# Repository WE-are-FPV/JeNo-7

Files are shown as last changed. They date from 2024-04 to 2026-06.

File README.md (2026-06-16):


> [!NOTE]
> Current version : **1.1.1** (read [changelog](#changelog) for details)

<!--![JeNo - Front view](./images/JeNo7_CloseProfileHeader.jpg)-->

# JeNo 7"
***7" drone FPV frame compatible with Air Unit O3 and O4 Pro, designed for LR, Cinematic, Freeride and even Freestyle. Many customizable options available.***

> [!NOTE]
> Designed in France by members of the [WE are FPV](https://www.wearefpv.fr/) community. The French version of the project is available on [Printables](https://www.printables.com/fr/model/847975-jeno-7-drone-frame). Note that a [2.5" version](https://github.com/WE-are-FPV/JeNo-Pocket), [3-3.5" version](https://github.com/WE-are-FPV/JeNo-3-3.5) and a [5.1-6" version](https://github.com/WE-are-FPV/JeNo-5.1) of the JeNo exist.

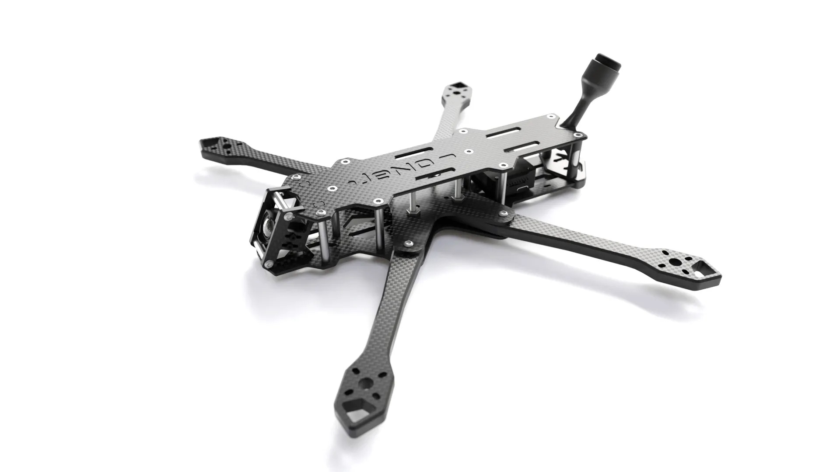
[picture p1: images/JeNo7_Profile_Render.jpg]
JeNo classic - 3D render


## Table of contents

* [Key features](#key-features)
* [Presentation](#presentation)
* [Detailed specifications](#detailed-specifications)
* [Versions and files](#versions-and-files)
* [Customization](#customization)
* [Cut it !](#cut-it-)
* [Bill of materials](#bill-of-materials)
* [Building/Assembly guide](#buildingassembly-guide)
* [Inspiration](#inspiration)
* [Tuning, Betaflight Preset ?](#tuning-betaflight-preset-)
* [Blackbox](#blackbox)
* [Videos](#videos)
* [Builds examples](#builds-examples)
* [Authors](#authors)
* [TPU](#tpu)
* [Community (remixes and TPU)](#community-remixes-and-tpu)
* [Changelog](#changelog)

## Key features
- [x] **Sturdiness** and **rigidity** (6 or 8 mm arms)
- [x] Designed as a **real 7"**, not 5" conversion
- [x] Excellent flight **performances**, easy to tune
- [x] **Wide-X** geometry
- [x] Perfect DJI **Air Unit O3 or O4 Pro** camera integration
- [x] Designed for : DJI Vista/AU O3/AU O4 Pro, WalkSnail, HDZero, Analogic
- [x] **Frame and standoffs NOT visible** in video feed, with any FPV camera
- [x] Stack **decoupled** from the arms
- [x] **Easy maintenance** : remove 3 screws to replace an arm
- [x] **Roomy** (30 mm high)
- [x] **Customizable** (arms thickness, camera plates)

## Presentation
Building on the success of the [5.1-6" version](https://github.com/WE-are-FPV/JeNo-5.1) and [3-3.5" version](https://github.com/WE-are-FPV/JeNo-3-3.5) versions, the **JeNo lineup** expands with this new variation in **7-8"**. We stay true to the JeNo spirit, offering a **versatile frame** that is perfect for **Long Range, cinematic**, and even **Freestyle** use, thanks to its strength and flight performance.

Given the limited options in the **Open Source** community for 7", especially for DJI O3/O4 Pro setups, we wanted to provide the community with a solid new option that caters to various needs while remaining true to the **"JeNo philosophy"** :

* **Clean Black Box** for easy tuning
* **Modularity**, with **8mm arms** (or 6mm with reinforcements) and a wide range of camera plates:
  - Classic at 25°
  - High tilt at 40°
  - Cinematic with clean FOV ("Wide") / 25° tilt (hard or soft)
  - Cinematic with clean FOV ("Wide") / 40° tilt
* Frame and standoffs invisible in the video feed with all cameras
* **100% clear FOV** with DJI O3/O4 Pro setups with cinematic camera plates (no frame or propellers visible)
* **Wide X** geometry for better flight feel
* Comfortable body for lipos up to over 6S / 3000mAh (+140mm available)

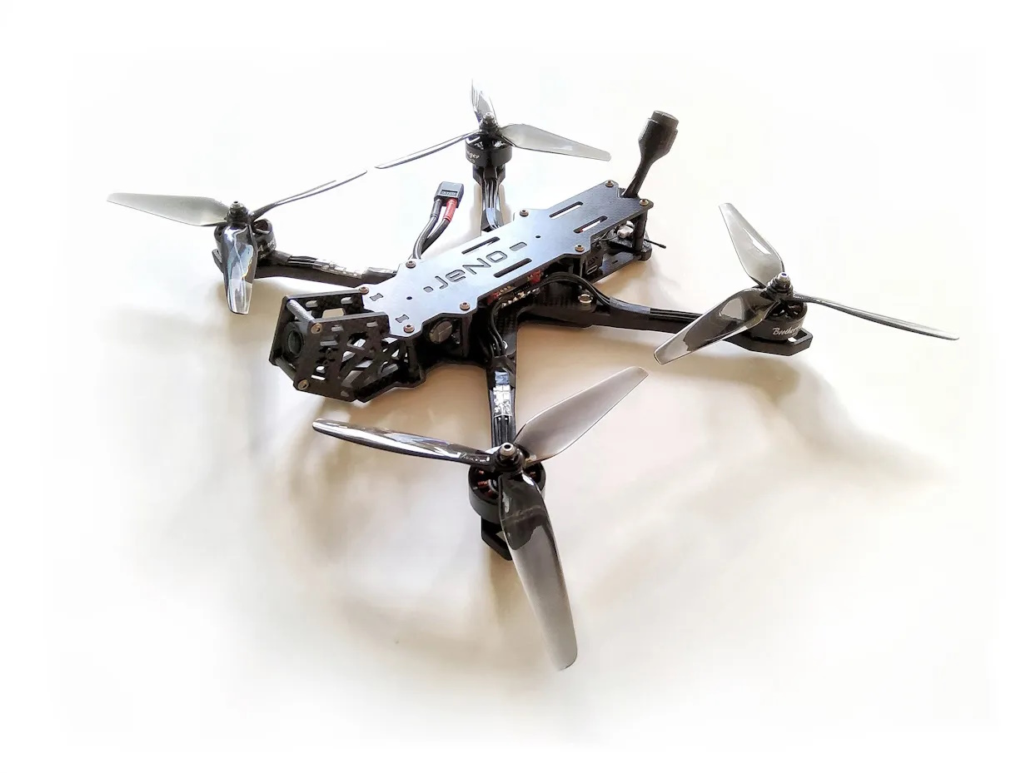
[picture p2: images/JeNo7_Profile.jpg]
JeNo 7 Profile


Finally, since this frame was designed by members of the [WE are FPV](https://www.wearefpv.fr/) **community**,  the "WaF" logo is engraved under the bottom plate (feel free to keep it or not). Join us on the WAF forum in [the official JeNo 7" thread](https://forum.wearefpv.fr/topic/22687-jeno-7/) to discuss it further.

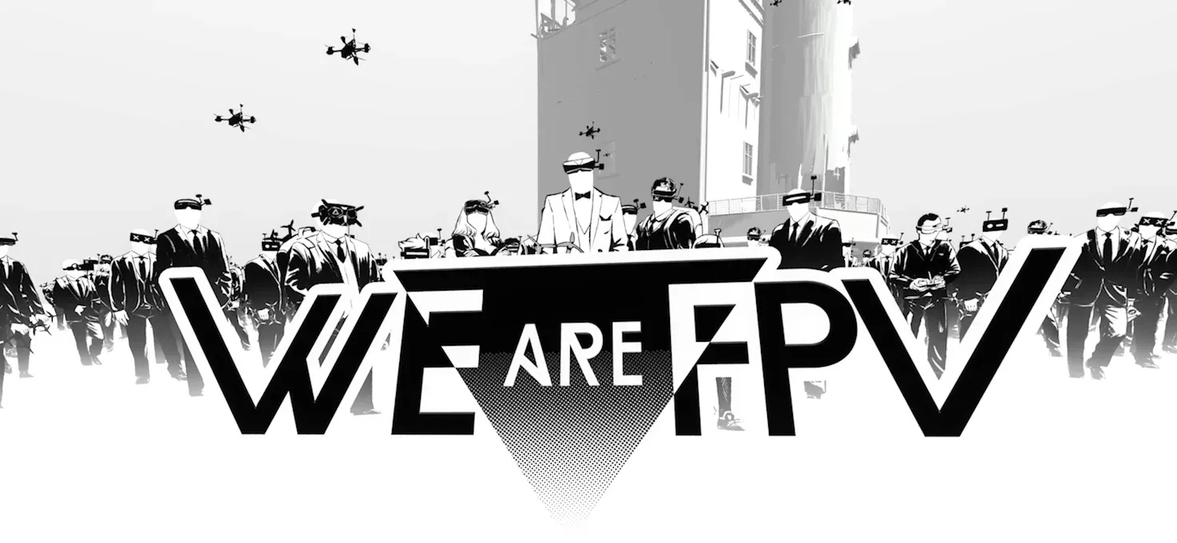
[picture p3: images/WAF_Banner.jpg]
WE are FPV banner


The JeNo is also available in [2.5" version](https://github.com/WE-are-FPV/JeNo-Pocket), [3" and 3.5" version](https://github.com/WE-are-FPV/JeNo-3-3.5) and [5.1" and 6" version](https://github.com/WE-are-FPV/JeNo-5.1).

## Detailed specifications

||| 
| :--- | :--- |
| **Geometry** | **Wide-X** | 
| **Props size** | 7" | 
| **Weight** | **248 to 260 g** depending on the versions, including screws | 
| **Arms** | **6 mm** (with 4mm reinforcements), **8mm** | 
| **Body height** | 30 mm | 
| **Stack height** | 19.5 to 21.5 mm depending the arms heights | 
| **Bottom plate** | 3mm | 
| **Middle plate** | 2.5 mm | 
| **Top plate** | 2.5 mm | 
| **Camera plates** | 3 mm | 
| **Motors mounting** | 16 to 19 mm | 
| **Camera** | 20 mm (DJI), Micro, Nano. **Clear FOV**. Ajustable.
| **Main stack** | 30 mm x 30 mm (M3) and 20 mm x 20 mm (M3) stack | 
| **Back stack** | 20 mm x 20 mm and 25 .5 x 25.5 mm | 
| **Supported VTX** | Analogic, DJI Vista, DJI Air Unit O3/O4 Pro, WalkSnail, HDZero… | 
| **Strap passage** | Yes | 

## Versions and files

### Versioning
You will find the **current version** of the frame at the beginning of the description and the full [history of modifications](#changelog) at the end of the page.

We strongly recommend always cutting the latest version to ensure you benefit from the most recent optimizations.

The version **number format** is as follows :
```
<Major versions>.<Minor version>.<Revision>
ex : 1.3.2
```

* **Revision :** This number is incremented in the case of minor modifications with no significant impact.
* **Minor version :** This number is incremented for minor modifications that may potentially break compatibility with certain TPU parts.
* **Major version :** This number is incremented for significant modifications that break compatibility at the carbon level.

Since the creation of the JeNo 7", we have always strived to **maintain compatibility at the carbon level**. As a result, the version remains “1.x.y.”

In practical terms, this means that if you have the very first version of the JeNo 7" and want to equip it with the **O4 Pro**, you only need to have new camera plates cut—they will be compatible with your frame version!

**Note :** If you develop TPU parts for the JeNo, be sure to specify the version they are compatible with.

### Files management
To simplify things, we have reorganized the file structure. The files are now divided into **five groups** :

* **01-FRAME :** Contains **models** describing the **frame** in DXF, STEP, and STL formats for the current version. Also contains a PDF file which is a reformatted version of the DXF.
* **02-TPU :** Contains **TPU models** for the current frame version in STL format.
* **03-FRAME-HISTORY :** Contains previous versions of the frame.
* **04-TPU-HISTORY :** Contains TPU models that are no longer compatible with the current version.
* **OTHER-FILES :** Contains documentation files. No assembly manual at the moment, but can check the [assembly guide of the JeNo 5"](https://github.com/WE-are-FPV/JeNo-5.1/tree/main/OTHER-FILES) which is very similar.

The major change is that all options are now consolidated into a single file. This will make version management significantly easier for us.

If you want to view the DXF file with all annotations, we recommend using the free software [DWG TrueView](https://www.autodesk.com/products/dwg-trueview/overview). If you prefer not to use it, the PDF version of the file will contain all the necessary information.

## Customization
As usual, this JeNo is **customizable** : it offers several **options** to best adapt to different needs and preferences.

### The arms
> [!TIP]
> We **strongly recommend** having the version with **8mm** arms cut (see Black Box a little further down). 

However, the version with 6mm + reinforcements remains entirely viable in case you have constraints on the availability of 8mm carbon.

The weight of the two versions remains very similar.

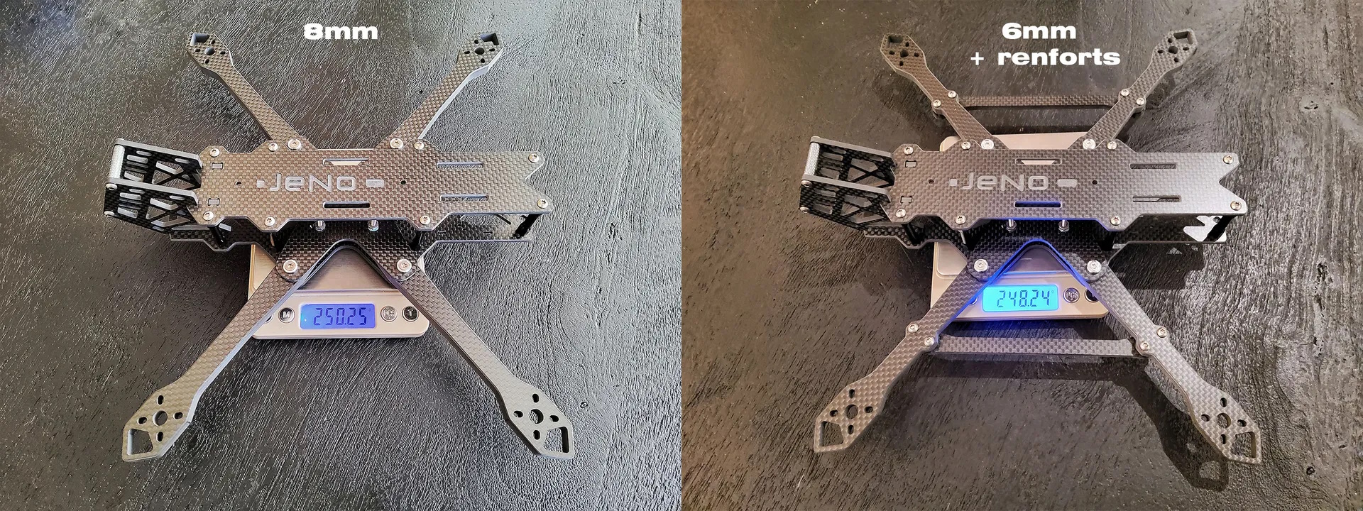
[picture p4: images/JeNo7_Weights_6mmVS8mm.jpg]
JeNo 7 weights


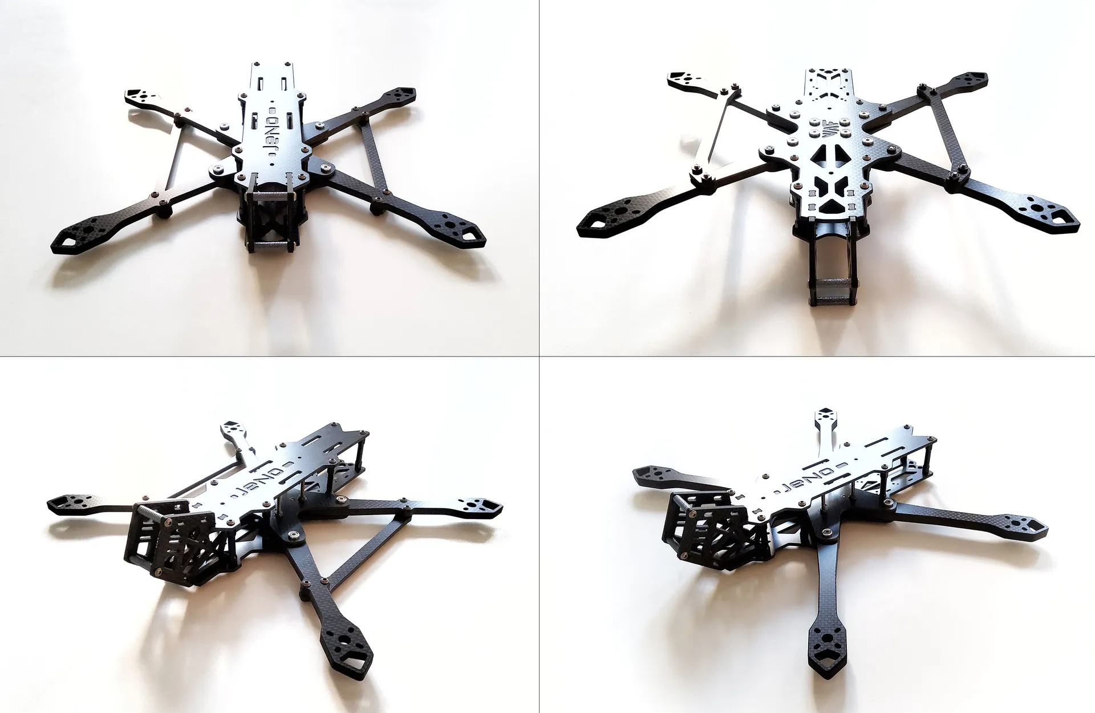
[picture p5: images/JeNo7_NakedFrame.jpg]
JeNo 7 verions


### Camera plates and O3 integration

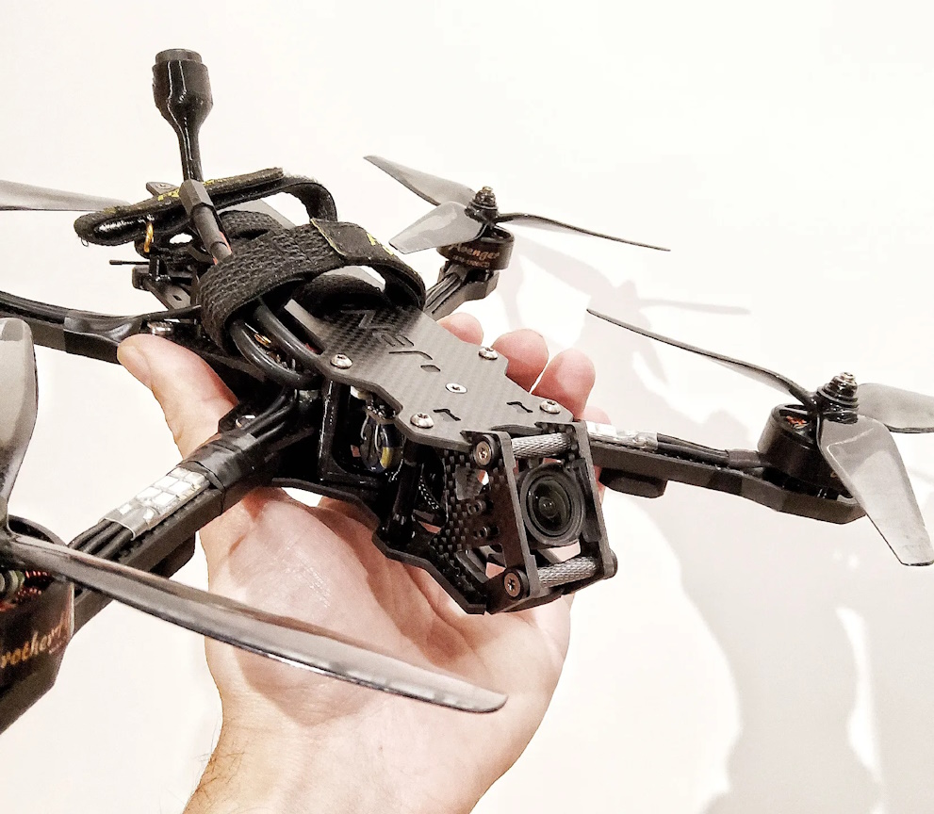
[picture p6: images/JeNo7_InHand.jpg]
JeNo 7 Cmera Plates


> [!CAUTION]
> The use of a 200mm coaxial cable for the O3 camera is mandatory.

Remarks regarding the **PWM frequency** of ESCs:

* **DJI recommends** using a PWM frequency of **48 kHz** or higher for effective stabilization
* However, a PWM frequency of **24 kHz is generally recommended for 7"**
* We have not observed stabilization issues while remaining at 24 kHz, even with a "hard mounted" camera. Therefore, we encourage you to test 24 kHz before anything higher.

Comparison of **FOV settings** with specific 7" Cinematic camera plates (Ultra Wide vs Wide):

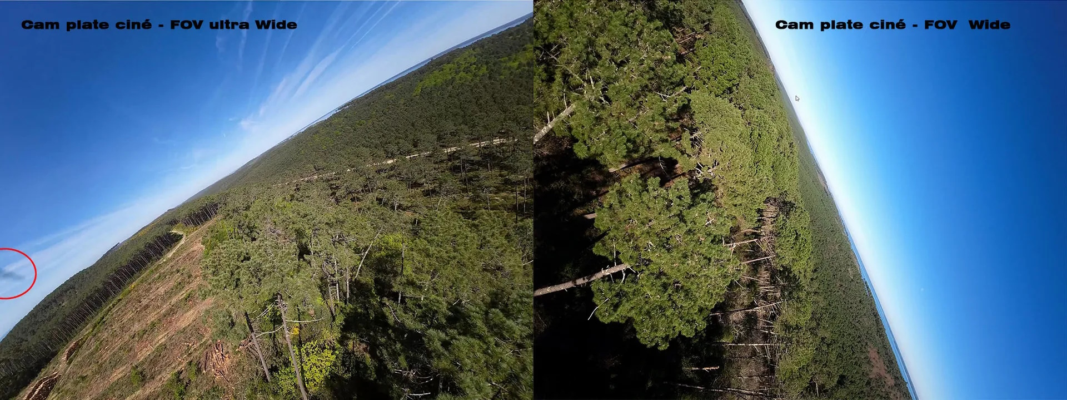
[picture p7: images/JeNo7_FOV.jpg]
JeNo 7 Camera Plates


The "cinematic" camera plates will allow you to enjoy a completely clear FOV (set as **Wide** in the O3) (and consequently, after stabilization).

Several types of camera plates are available, so you will need to **choose** the type of camera plate that best suits **your needs**.

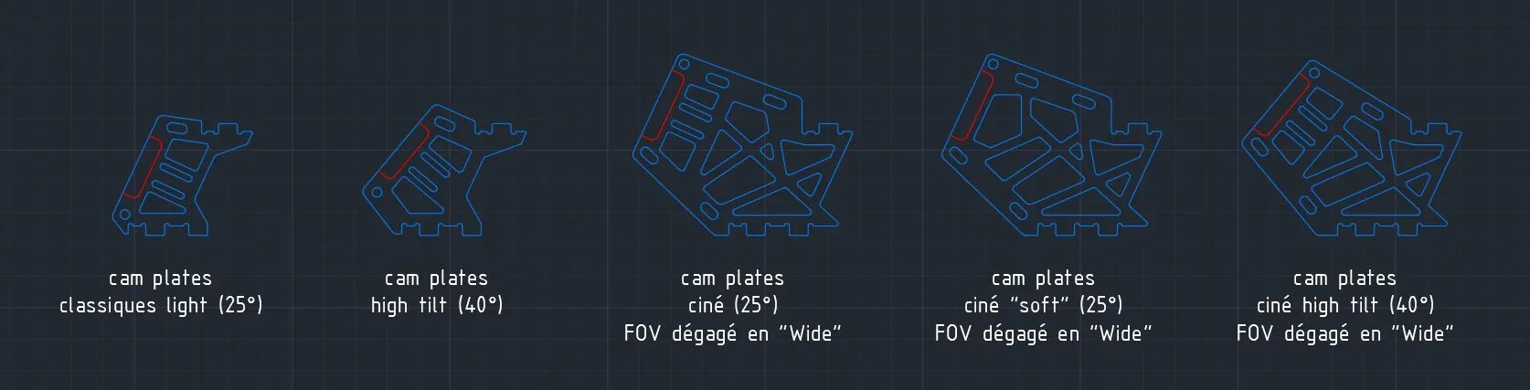
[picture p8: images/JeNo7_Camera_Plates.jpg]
JeNo 7 Camera Plates blue prints


## Cut it !

The JeNo 7" is available from [CNC Madness](https://cncdrones.com/jeno-7-inch.html) (Canada) and [FPV CNC Drone](https://fpvcncdrone.com/) (France).

The ["01-FRAME"](https://github.com/WE-are-FPV/JeNo-7/tree/main/01-FRAME) folder contains all the files you need to get it **cut** in your favourite flavour.

Consult the **DXF file** of the frame (or the PDF version) to choose the version that interests you.

Feel free to select a pre-made "Edition" (Classic, Light, or Bando), or mix different options and choose certain "extras".

You will also need to choose a type of camera plates (classic, cine, etc.).

> [!NOTE]
> All parts versions are compatible with each others

## Bill of materials

In addition to the carbon fiber, you will need the following hardware to complete the assembly of the frame.

**Standoffs**

It is recommended to use 5mm diameter standoffs, especially for those that will serve as support for TPU (backpack and capacitor). Moletted spacers can still be used, but the TPU supports will need to be modified accordingly.

| Quantity | Description | Details |
| :---: | :--- | :--- |
| 10 | M3x30mm standoffs | for the body |
| 2 (or 4 for cinematic plates) | M3x20mm standoffs | for the camera |

**Stack materials**

* If 30x30 stack

| Quantity | Description | Details |
| :---: | :--- | :--- |
| 4 | M3x20mm countersunk screws | for the stack |
| 4 | M3 nuts for stack screws | |

* If 20x20 stack

| Quantity | Description | Details |
| :---: | :--- | :--- |
| 4 | M3x20mm countersunk screws | for the stack |
| 4 | M3 nuts for stack screws | |

**Frame materials**

| Quantity | Description | Details |
| :---: | :--- | :--- |
| 6 | M3x6/8mm countersunk screws | for the top plate |
| 4 | M3x6/8mm screws | for the top plate |
| 10 | M3x8mm screws (titanium if possible) | Bottom plate |
| 4 (or 8 for cinematic plates) | M3x6/8mm screws (titanium if possible) | Camera plates |
| 12 | Pressnuts ([Flywoo](https://www.drone-fpv-racer.com/flywoo-m3-clinch-nuts-20-pcs-7965.html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) or SourceOne alike) | |
| 4 | M3x18mm countersunk screws + washers or M3x16mm screws (steel if possible)  | for the arms (2 mm shorter for 6mm arms) |
| 4 | M3x12mm countersunk screws + washers or M3x10mm screws (steel if possible) | for the arms (2 mm shorter for 6mm arms) |

**Additional materials 6mm amrs  renforcements**

| Quantity | Description | Details |
| :---: | :--- | :--- |
| 8 | Pressnuts ([Flywoo](https://www.drone-fpv-racer.com/flywoo-m3-clinch-nuts-20-pcs-7965.html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) or SourceOne alike) | 2 per arm) |
| 8 | M3x12mm screws | 2 per arm |

**Additional materials**

| Quantity | Description | Details |
| :---: | :--- | :--- |
| 16 | M3x12mm screws (if using arms protections) or M3x8mm (if no TPU) | for the motors (2 mm shorter for 6mm arms) |
| 4 | M2x5mm screws | for the camera |

**Fasten the lipo**

The JeNo allows the use of non-slip straps thanks to its strap slots. You can also use a LiPo pad if desired.

## Building/Assembly guide

Find numerous examples of builds on the _**DroneBuilds**_ page of WE are FPV.
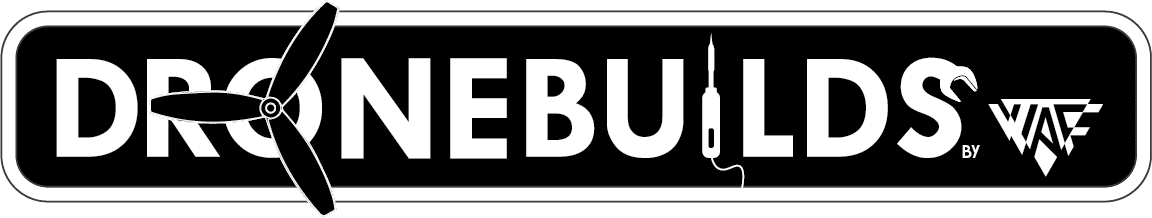
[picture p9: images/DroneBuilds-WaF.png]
DroneBuilds (https://forum.wearefpv.fr/71-dronebuilds/ "DroneBuilds - Click to Access!")


The assembly of the frame is straightforward; however, a few clarifications:

* On one of the two sides of the **middle plate**, there are countersunk holes to accommodate countersunk screws. This side corresponds to the **underside**. Do not forget to install the stack screws before installing the middle plate.
* The pressnuts will be positioned on the underside of the bottom plate.
* An RX T antenna can be fixed to the rear of the JeNo using zip ties.
* Six screws of the top plate are countersunk screws to avoid damaging the battery.

## Inspiration
The JeNo 7" takes inspiration from the path laid out by the [KayouLoin](https://kayou-frames.com/fr/frames/25-kayouloin-7-frame.html).

While implementing 8mm arms remains quite evident, the KayouLoin innovates by introducing a **body that matches the quad's proportions**.

Certainly, this adds weight, but it provides the frame with unparalleled comfort in accommodating suitable batteries and absolute rigidity. If the cutting and sourcing of hardware are too constraining for you, we advise you to go directly to [Kayou's website](https://kayou-frames.com/fr/) !

## Tuning, Betaflight Preset ?
We probably won't provide a preset because motor setups have a huge influence, but here are some recommendations from Mark Spartz for 7" setups:

* ESCs PWM Frequency at **24KHz**
* **Reduce I** compared to a 5" (start with the slider at 0.5)

## Blackbox

Here is an overview of vibration distribution on the 3 axes for the JeNo 7". On the right with 6 mm arms (+ reinforcements), on the left with 8 mm arms. This is indeed the **unfiltered** gyro signal for a 3 minutes freestyle flight :

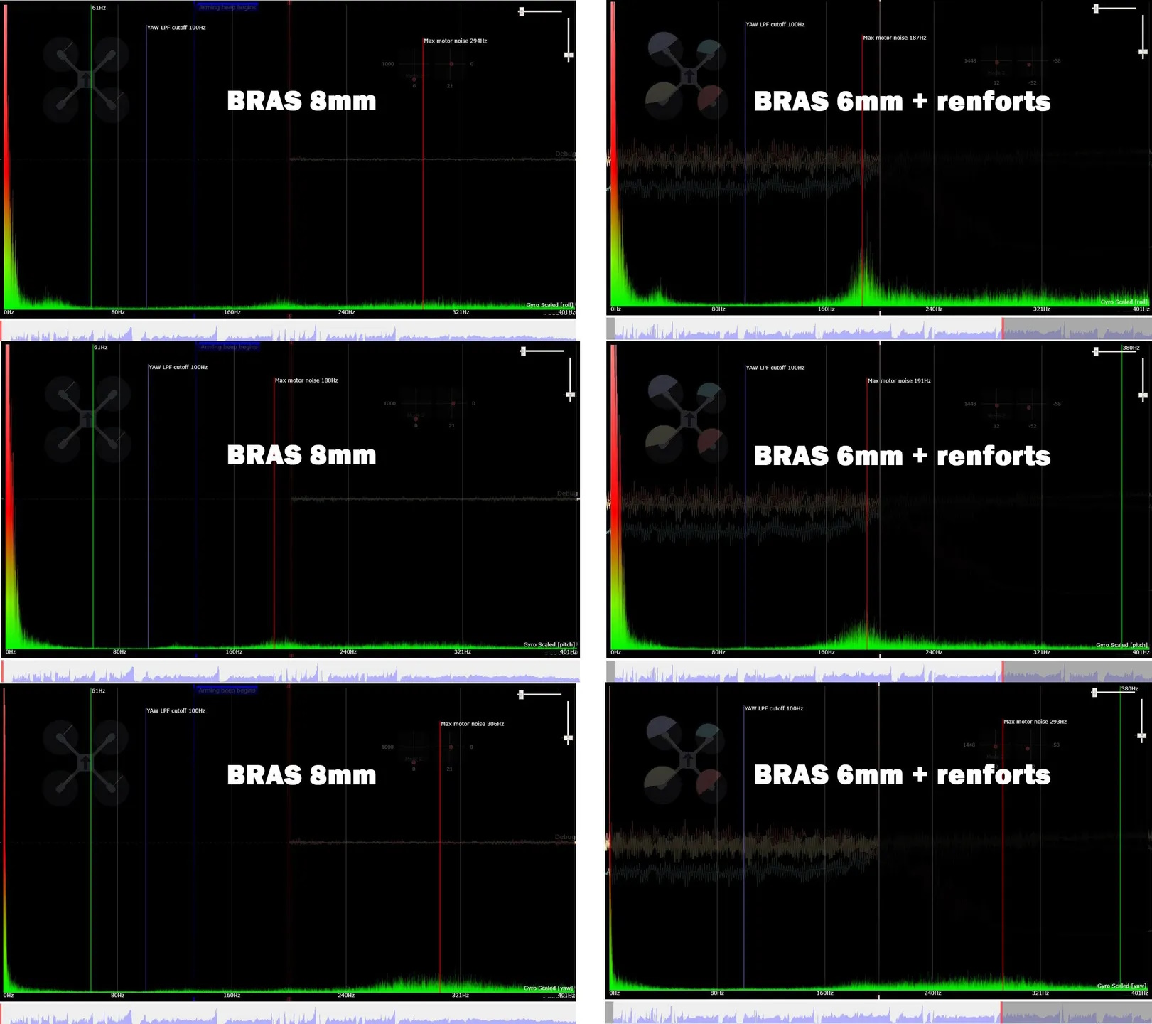
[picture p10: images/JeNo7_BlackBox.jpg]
JeNo 7 Blackbox


## Videos
Freestyle with JeNo :

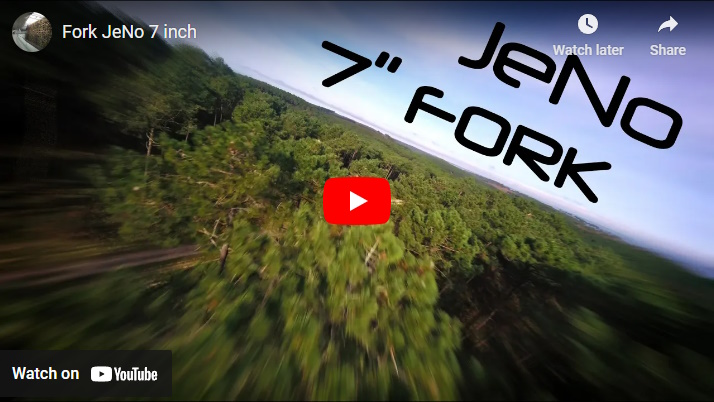
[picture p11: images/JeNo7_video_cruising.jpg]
JeNo 7" Maiden (https://www.youtube.com/watch?v=4mE-WnIyyHg "JeNo 7 Maiden - Click to Watch!")


## Builds examples
You can find build examples on [WE are FPV's DroneBuilds](https://forum.wearefpv.fr/71-dronebuilds/) :

* fr : [JeNo 7" Fork](https://forum.wearefpv.fr/topic/22645-jeno-7-fork)

## Authors

The JeNo was designed by :

* nochamo - [Youtube](https://www.youtube.com/user/nochamo)

## TPU
For now, a [minimalist TPU kit](https://github.com/WE-are-FPV/JeNo-7/tree/main/tpu) is available to you, containing:

* O3 antenna mount
* Double SMA Antenna Support
* 50V capacitor mount + spike absorber
* Rear bumper + RX antenna mount
* Front RX Support
* Arm protection with skids (6 and 8mm)

This offering **will expand** over time thanks to the community.

## Community (remixes and TPU)

**Fork/remix**

* [JeNo 7" Freestyle (Bash Edition)](https://www.printables.com/model/1073983-jeno-7freestyle-bash-edition), a mix between the JeNo 7" and the [JeNo PlatyStyle](https://www.printables.com/model/744619-jeno-51-platystyle-edition), otpimised for freestyle, by [Bash FPV](https://www.youtube.com/watch?v=s_6Gz9fyeIc&ab_channel=BashFPV)
* [JeNo 7" BBL - Freestyle Bando - RanxFPV Edition](https://www.printables.com/model/1411549-jeno-7-bbl-freestyle-bando-ranxfpv-edition), a mix between the JeNo 7" and the remix from Bash FPV, for freestyle and bando (O3 and O4 Pro compatible), by [RankFPV](https://www.youtube.com/@RanxFPV)

**TPU**

In addition to the TPU options available on this page, you will find here some TPU designs created by the community.

* [Full TPU set](https://www.printables.com/fr/model/911148-jeno-7-tpu-kit-complet), [immortal-T antenna support](https://www.printables.com/fr/model/914154-jeno7-antenne-immortal-t) and a [DJI Action 2 mount](https://www.printables.com/fr/model/918051-jeno-7-dji-action-2-mount-25deg-filtre-nd-tbs) designed by [Jean-Lil](https://www.printables.com/fr/@JeanLil_707453)
* [Full TPU set, compatible with COB LEDs](https://makerworld.com/en/models/551901) by [BinaryWhite](https://www.youtube.com/@focal3drone803) (many TPUs are available, including RX and GPS mounts)
* [DJI Action 2 mount](https://www.printables.com/fr/model/960035-jeno-7-dji-action-2-mount-40deg-filtre-nd-tbs-batm) with a 40-degrees-tilt by [Lëtz Kwad](https://www.printables.com/fr/@LetzKwad_707453)

## Changelog

> [!TIP]
> Compatibility is consistently maintained between each version: if your frame was a v1, the parts from v1.2 will be compatible. The same applies to TPU accessories. That's why we don't keep the history of previous versions.

* 18/02/2025 :
  * Addition of TPU for softmounted camera plates (compatible with O4 Pro and O3)
* Version **1.1.1** (02/02/2025) :
  * Addition of cinematic and softmounted camera plates at 25° (for O4 Pro and O3)
* Version **1.1.0** (01/02/2025) :
  * Support for the Air Unit O4 Pro (camera plates)
* 21/05/2024 :
  * Addition of a top plate with XT60 cutout in the "extra" folder
* 04/06/2024 : 
  * Addition of 8" arms (untested) in the "extra" folder
* Version **1.0.0** (23/04/2024)

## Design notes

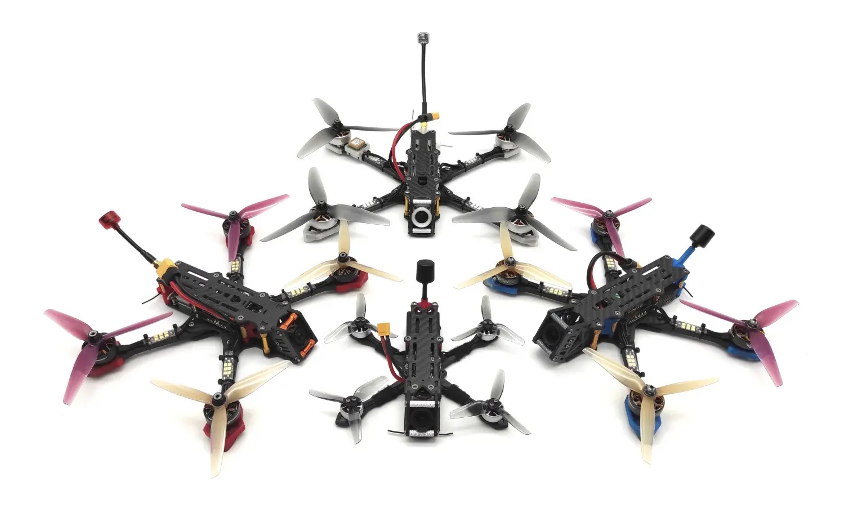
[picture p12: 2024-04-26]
images/JeNo_Family.jpg

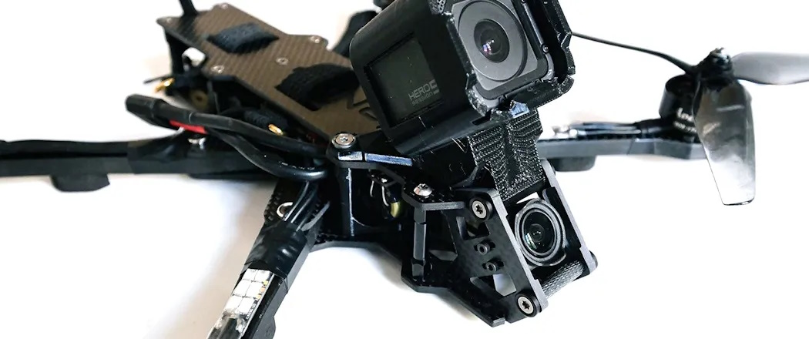
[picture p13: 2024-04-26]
images/JeNo7_CloseProfileHeader.jpg

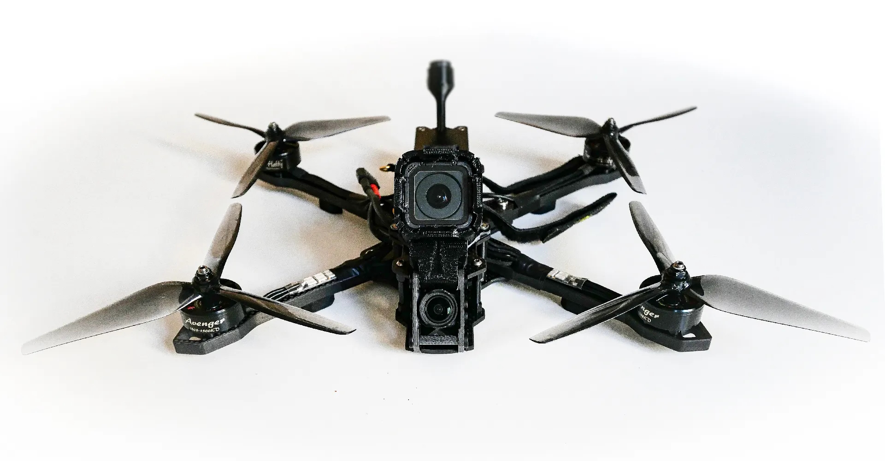
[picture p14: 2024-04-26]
images/JeNo7_TopFront.jpg

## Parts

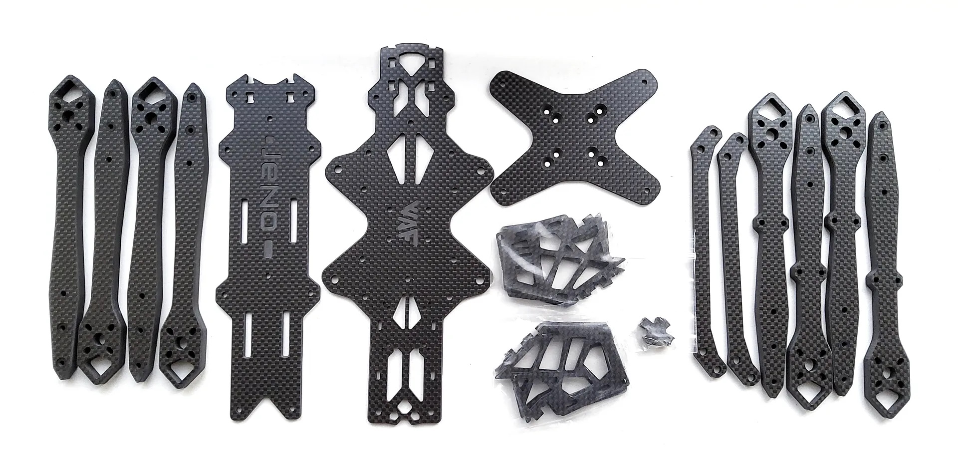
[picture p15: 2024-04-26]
images/JeNo7_Parts.jpg

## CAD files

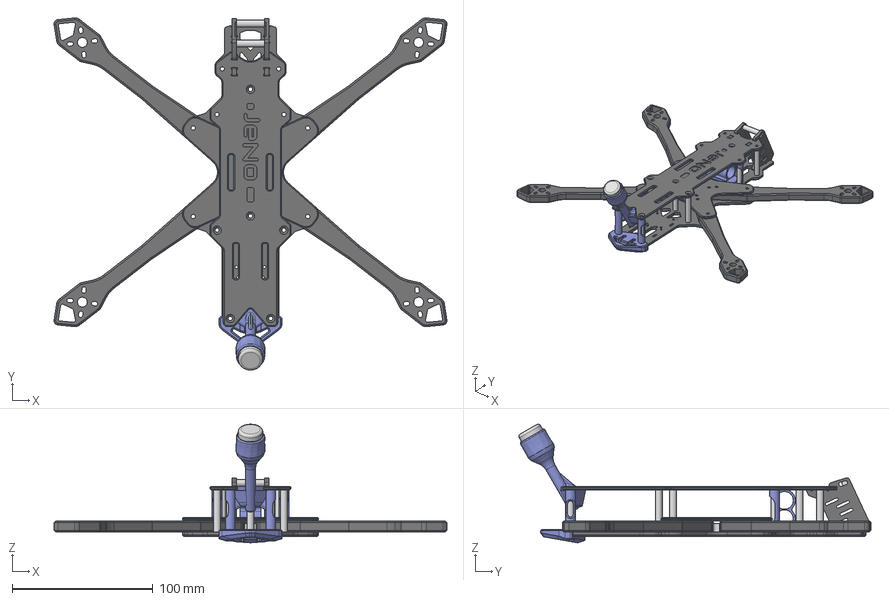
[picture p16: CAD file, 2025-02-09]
01-FRAME/JeNo7_ALL_VERSIONS_1.1.1.step
279.6 x 250.5 x 84.4 mm

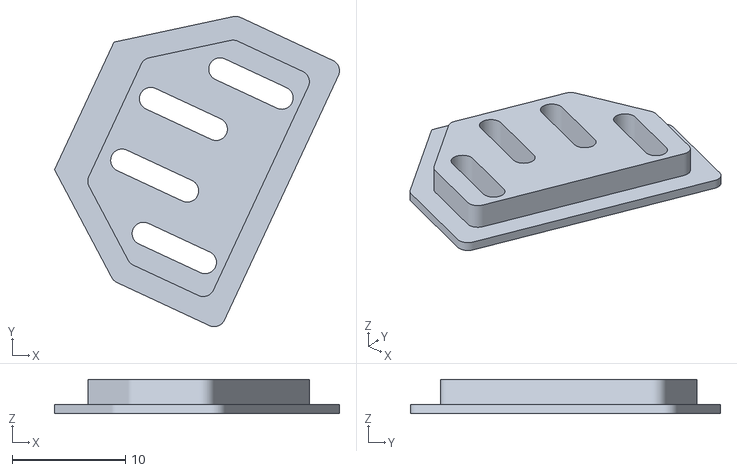
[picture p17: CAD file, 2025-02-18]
02-TPU/JeNo7_Soft_Mount_Cine_Plate_O3_O4.stl
25.1 x 27.4 x 3.00

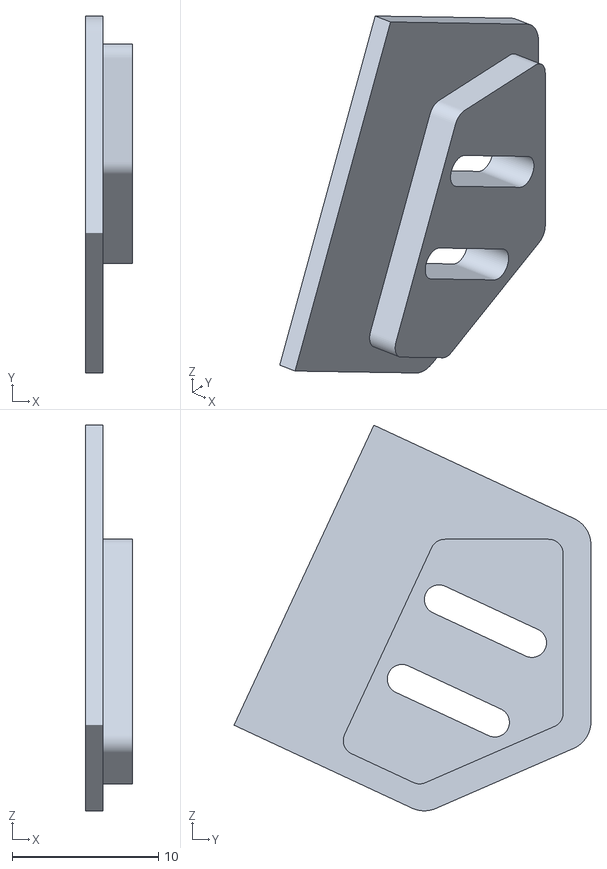
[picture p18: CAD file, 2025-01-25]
04-TPU-HISTORY/JeNo7_1.0.0_Soft_Mount_Cine_Plate.stl
3.20 x 24.4 x 26.4

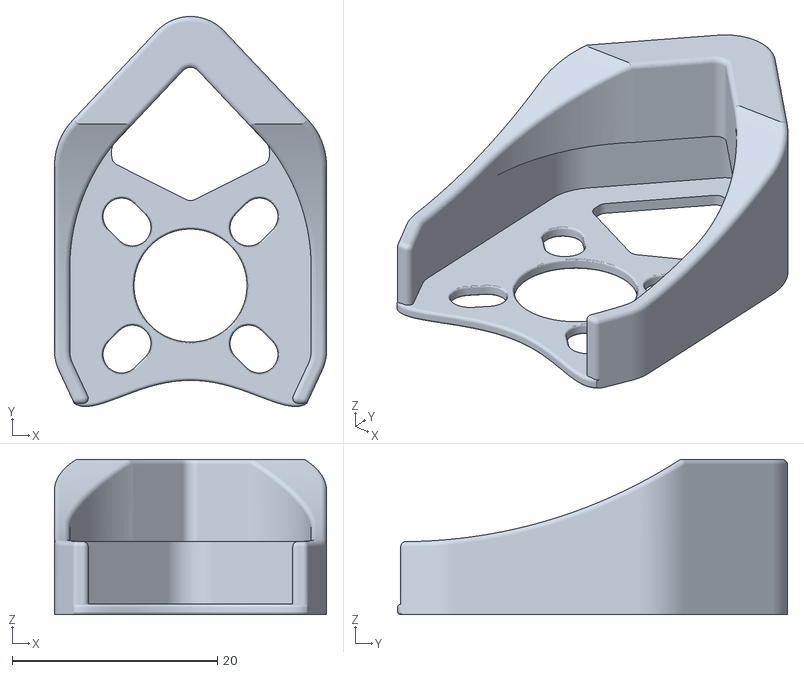
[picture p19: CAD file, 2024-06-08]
02-TPU/JeNo7_Arm_6mm.stl
26.5 x 38.0 x 15.1

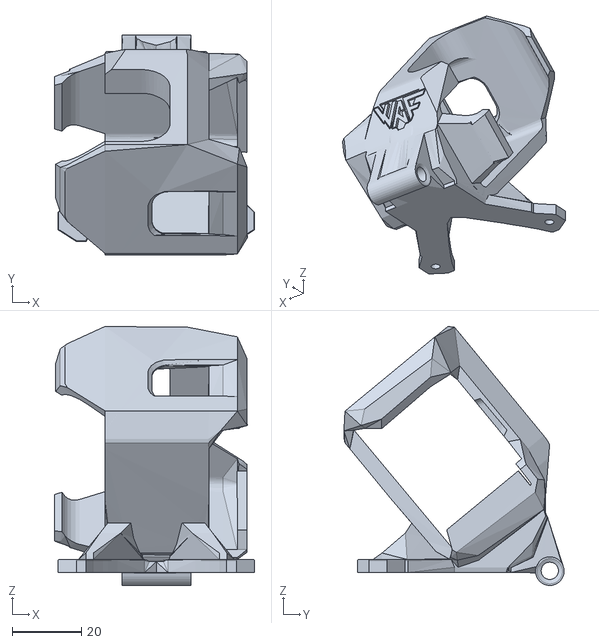
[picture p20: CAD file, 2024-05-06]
04-TPU-HISTORY/JeNo7_1.0.0_Gopro_Mini_40deg.stl
58.0 x 63.8 x 75.0

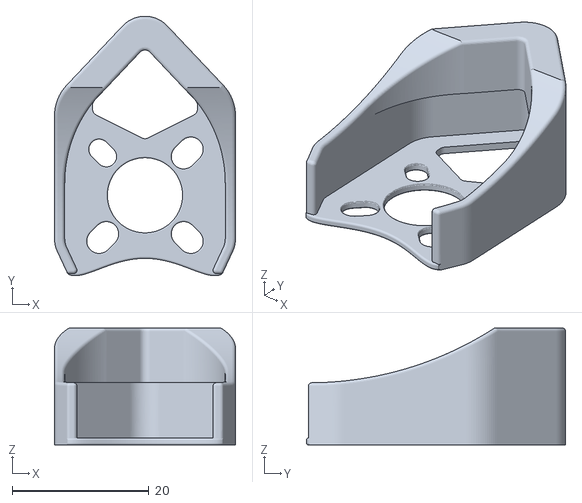
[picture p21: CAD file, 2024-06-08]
02-TPU/JeNo7_Arm_8mm.stl
26.5 x 38.0 x 17.1

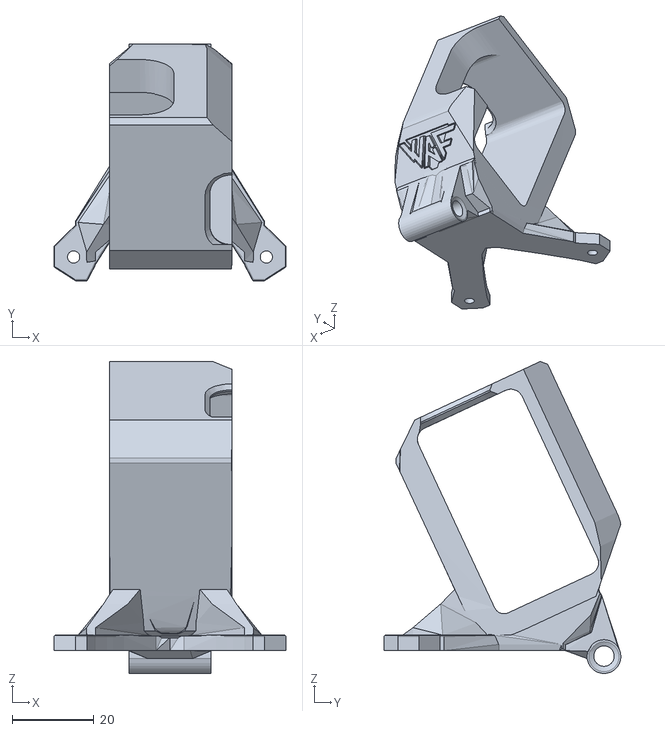
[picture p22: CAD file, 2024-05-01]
04-TPU-HISTORY/JeNo7_1.0.0_Gopro_25deg.stl
56.9 x 58.1 x 76.5

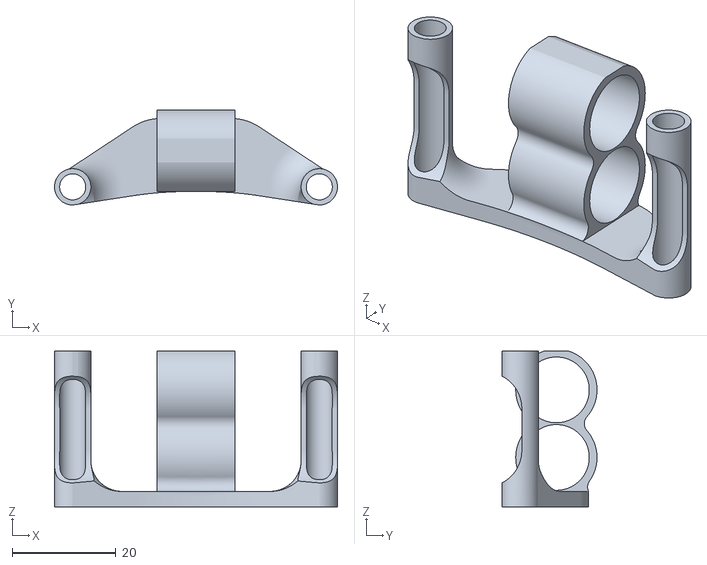
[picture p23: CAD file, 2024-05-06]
02-TPU/JeNo7_Capacitor_Support_35Vx2.stl
54.5 x 18.3 x 30.0

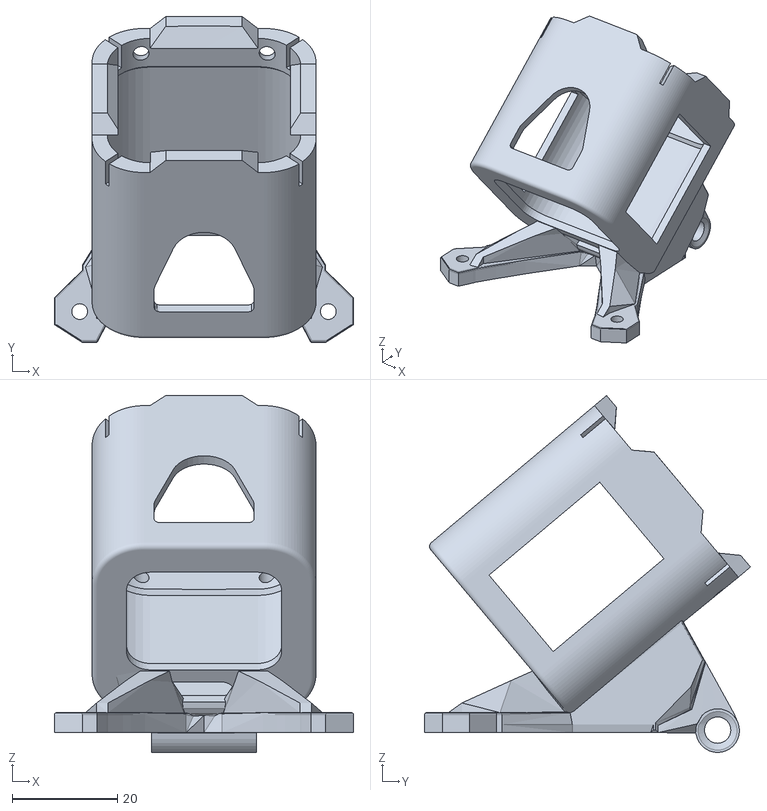
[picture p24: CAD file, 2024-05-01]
04-TPU-HISTORY/JeNo7_1.0.0_Session_High_Tilt.stl
56.9 x 62.0 x 67.9

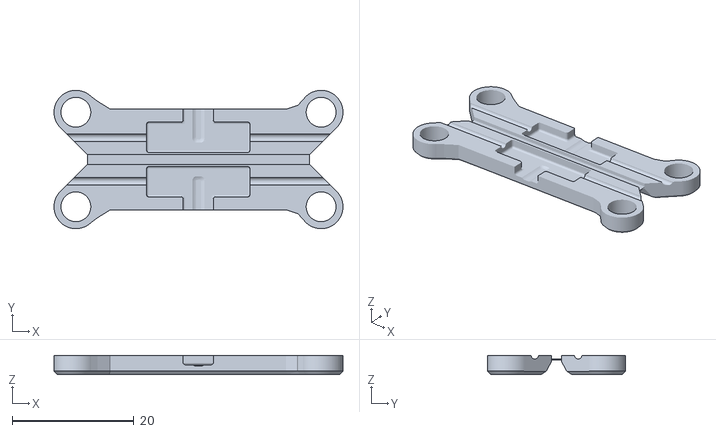
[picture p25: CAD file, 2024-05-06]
02-TPU/JeNo7_Antenna_Front_RX_Support.stl
47.5 x 22.7 x 3.20

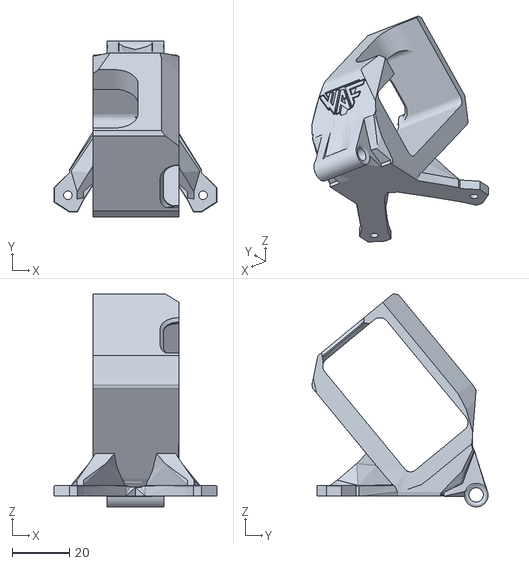
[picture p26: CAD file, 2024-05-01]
04-TPU-HISTORY/JeNo7_1.0.0_Gopro_40deg.stl
56.9 x 61.6 x 74.5

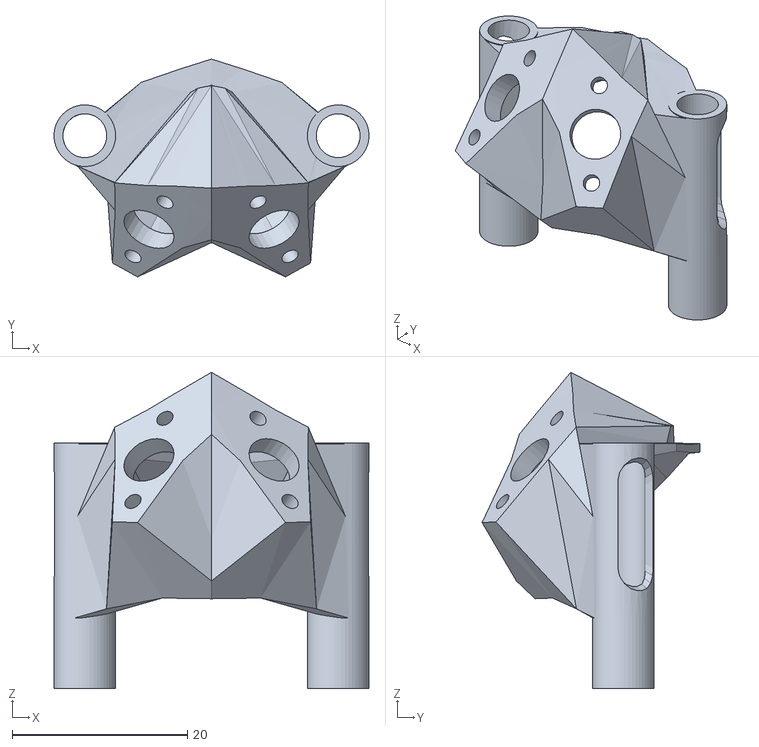
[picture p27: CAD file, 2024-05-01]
02-TPU/JeNo7_Antenna_Double_SMA.stl
35.9 x 24.8 x 36.1

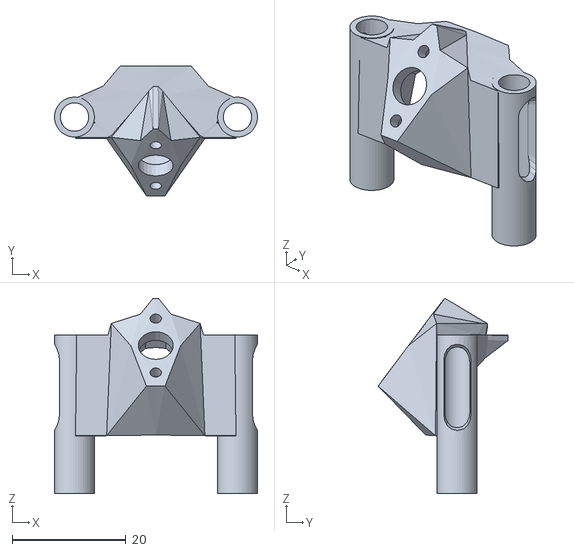
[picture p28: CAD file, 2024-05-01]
02-TPU/JeNo7_Antenna_SMA.stl
35.7 x 22.8 x 34.4

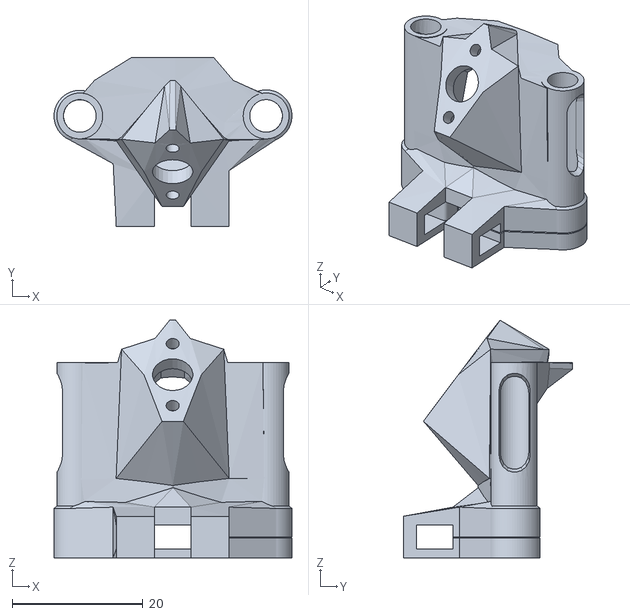
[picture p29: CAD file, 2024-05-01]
02-TPU/JeNo7_Antenna_SMA_T-Antenna.stl
36.4 x 25.9 x 36.4

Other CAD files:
dxf/JeNo_7_Full_8mm.dxf
03-FRAME-HISTORY/JeNo7_ALL_VERSIONS_1.0.0.dxf
01-FRAME/JeNo7_ALL_VERSIONS_1.1.0.dxf
02-TPU/JeNo7_Capacitor_50V_Spike_Support.stl
01-FRAME/JeNo7_ALL_VERSIONS_1.1.1.dxf
01-FRAME/JeNo7_ALL_VERSIONS_1.1.1.stl
02-TPU/JeNo7_Antenna_VTX_O3.stl
02-TPU/JeNo7_Back_Bumper.stl

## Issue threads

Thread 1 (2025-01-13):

O4 Camera plates

peterlozano, 2025-01-13:
Hi.

It would be great if someone could re-design the camera plates to allow the O4 mount.

Thanks.

LordGG, 2025-01-13:
Hi,

New camera plates for O4 are being tested for JeNo 3 and JeNo 5.  JeNo 7" will follow :)

Closed 2025-04-19.

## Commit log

2024-04-26 Load repo files from Printables
    [3D_JeNo_7pouces_8mm.step, 3D_JeNo_7pouces_8mm.stl, JeNo7_50VCap_Spike_Support.stl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]
2024-05-01 new STLs
    [JeNo7_Support_Double_SMA.stl, JeNo7_Support_SMA.stl, JeNo7_Support_SMA_T-Antenna.stl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]
2024-05-06 Ajout STLs
    [JeNo7_Cap_Support_35Vx2.stl, JeNo7_Front_RX_Antenna_Support.stl]
2024-06-08 arms protections
    [JeNo7_Arm_Protec_6mm.stl, JeNo7_Arm_Protec_8mm.stl]
2025-02-02 Version 1.1.0 : O4 Pro compatibility
    [3D_JeNo_7pouces_8mm.step, 3D_JeNo_7pouces_8mm.stl, JeNo7_ALL_VERSIONS_1.0.0.dxf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]
2025-02-09 1.1.1 update
    [JeNo7_ALL_VERSIONS_1.1.1.dxf, JeNo7_ALL_VERSIONS_1.1.1.step, JeNo7_ALL_VERSIONS_1.1.1.stl]
2025-02-12 deprecated models
    [JeNo7_1.0.0_Gopro_25deg.stl, JeNo7_1.0.0_Gopro_40deg.stl, JeNo7_1.0.0_Gopro_Mini_40deg.stl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]
2025-02-18 TPU for softmounted cam plates
    [JeNo7_Soft_Mount_Cine_Plate.stl, JeNo7_Soft_Mount_Cine_Plate_O3_O4.stl]
2025-09-02 Apply line ending normalization for DXF
    [JeNo7_ALL_VERSIONS_1.0.0.dxf, JeNo7_ALL_VERSIONS_1.1.1.dxf]

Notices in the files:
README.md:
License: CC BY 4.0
